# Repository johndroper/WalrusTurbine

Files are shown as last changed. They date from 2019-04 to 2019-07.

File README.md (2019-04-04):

# The Walrus Turbine Procedural Engine
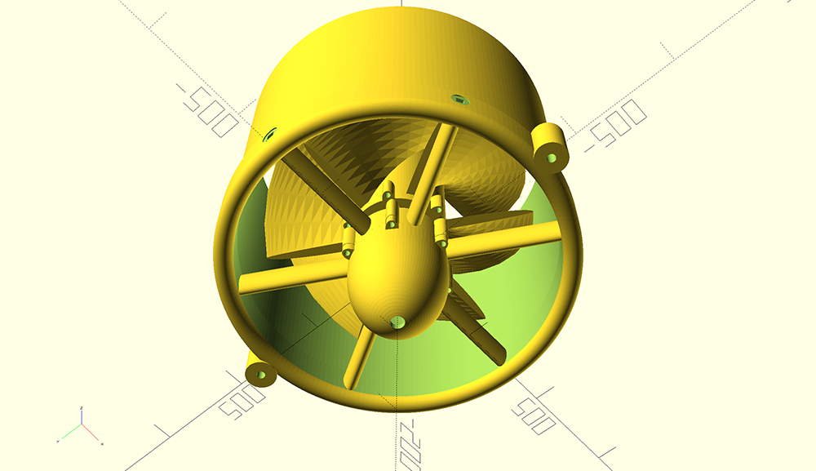
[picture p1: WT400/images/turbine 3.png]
Turbine


WalrusTurbine is a procedural engine for making mostly 3D printable mobile hydroelectric power generators.  

## Getting Started

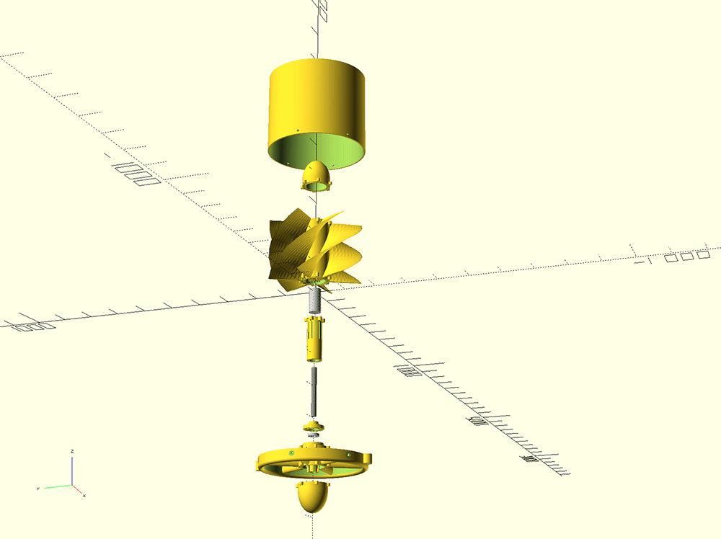
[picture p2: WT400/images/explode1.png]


### Prerequisites

The project is written in [OpenSCAD](http://www.openscad.org/).

### Installing

1. Put all .scad files in the same directory.
2. Open [assembly.scad](assembly.scad) in OpenSCAD to see the full assembled model.
3. Set the explode flag to 1, save, and have a look around. This may be just a wee bit taxing on your machine...

## Physical Assembly

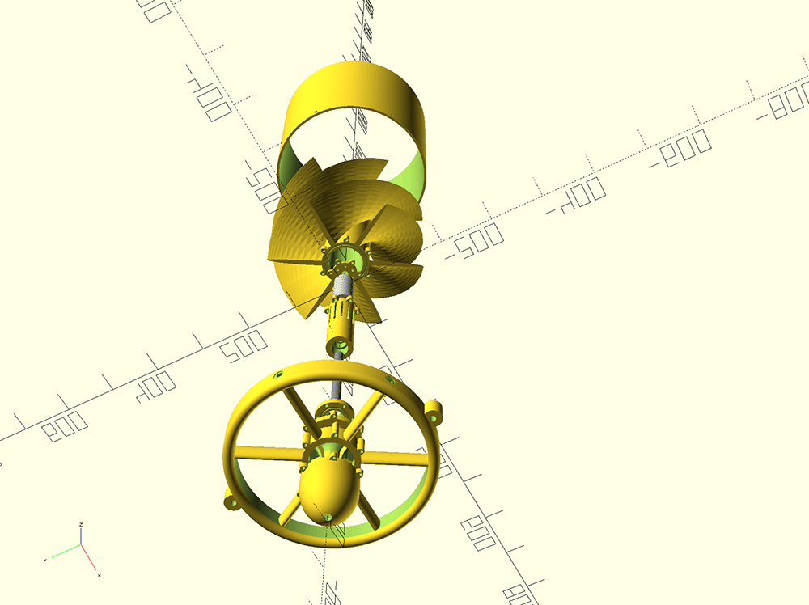
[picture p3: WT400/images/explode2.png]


The Walrus Turbine Procedural Engine was used create a denomstration model called the WT400. The WT400 is design to be printed on a printer with at least 400 mm build volume in all axis.

### Building a WT400
* [List of the non 3d printable parts and where to buy them.](WT400/parts-list.md)
* [Super rudimentary instructions.](WT400/instructions.md)

A lot more docs are coming soon so stay tuned.

## Contributing

Anyone who wants to contribute anything from openSCAD improvements to better assembly instructions is more than welcome.

## Authors

* **John Roper** 
* **Peter Brussard**

## License

This project is licensed under the MIT License - see the [license.txt](license.txt) file for details

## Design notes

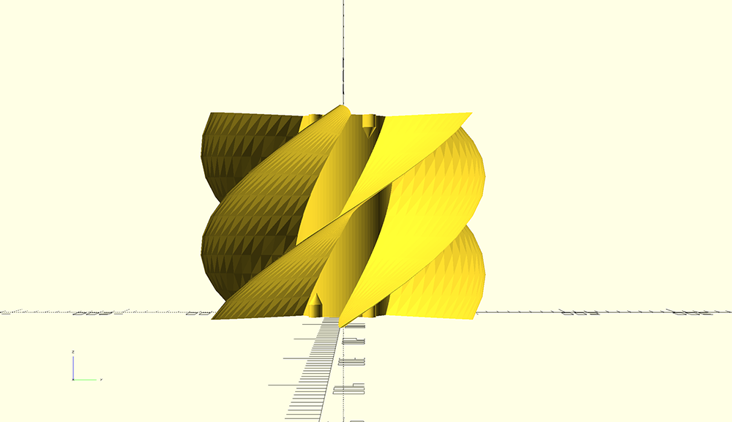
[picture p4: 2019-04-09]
WT400/images/runner front.png

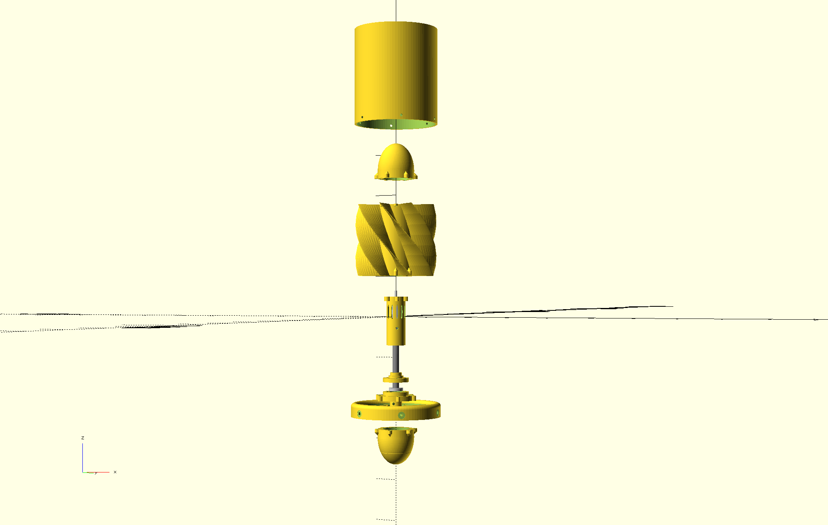
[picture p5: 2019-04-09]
WT400/images/explode 1.png

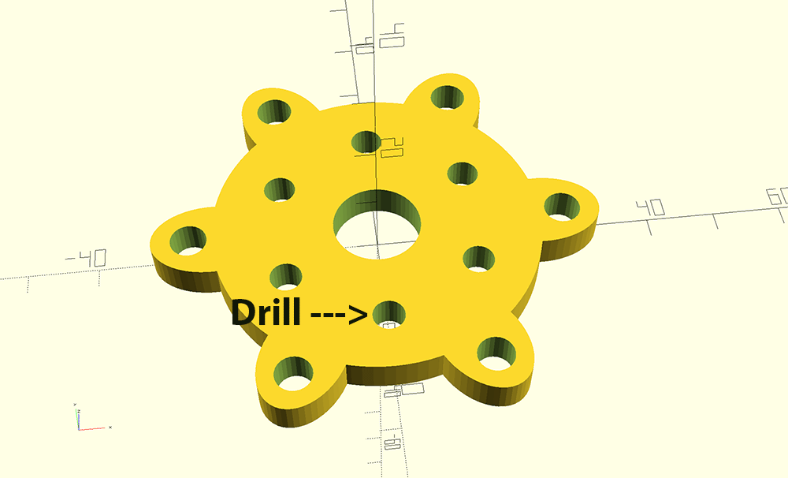
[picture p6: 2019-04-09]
WT400/images/drill_motor_mount_holes.png

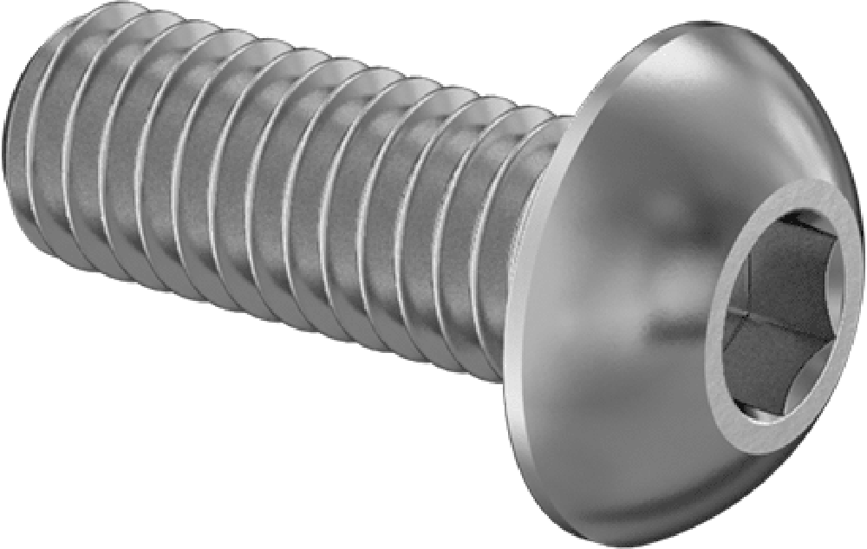
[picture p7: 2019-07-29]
WT400/images/M3_8mm_hex_screw_1000.png

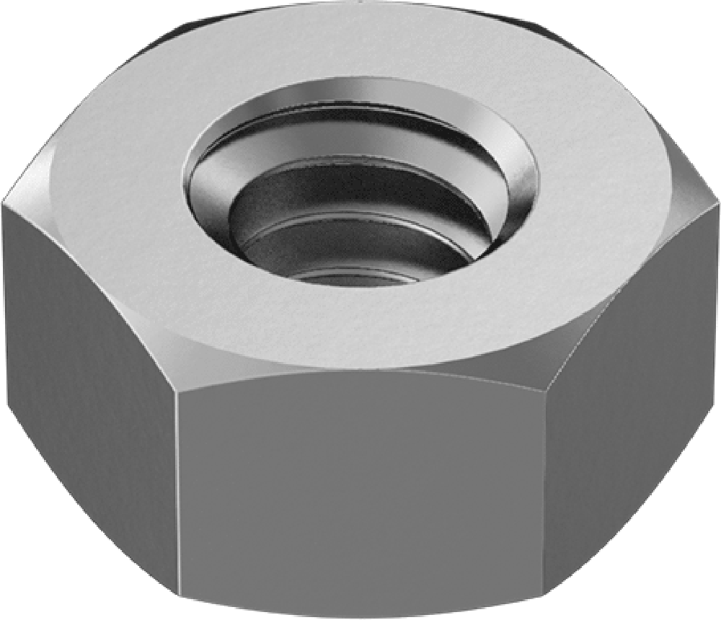
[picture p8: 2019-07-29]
WT400/images/hex_nut_1000.png

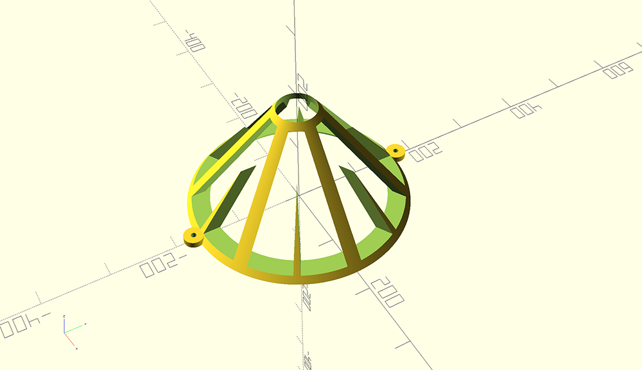
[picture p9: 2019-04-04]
WT400/images/guard.png

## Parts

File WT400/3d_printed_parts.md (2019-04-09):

# WT400 3D Printed Parts

## Parts
|  Part | Closeup  | 
| ---- | ---- |
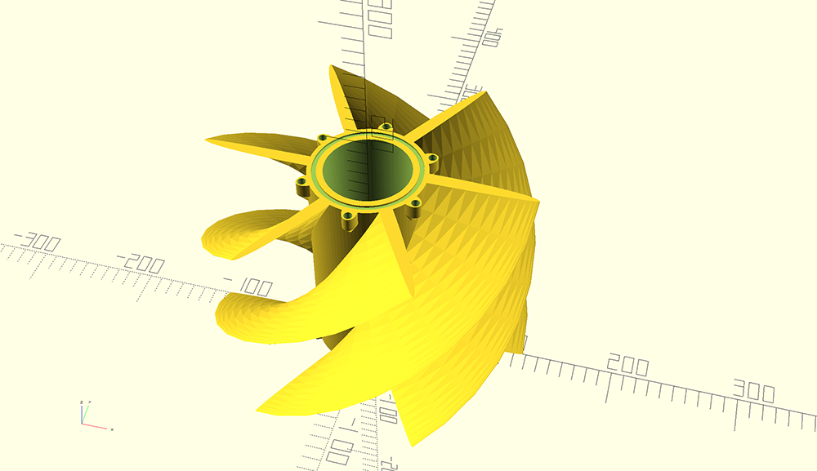
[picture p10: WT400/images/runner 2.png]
Runner
| <a id="runner">Runner</a> |  |
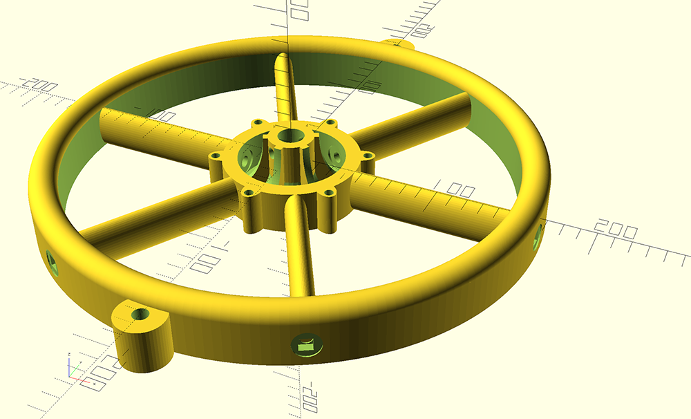
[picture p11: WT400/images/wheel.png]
Wheel
| <a id="wheel">Wheel</a> |  |
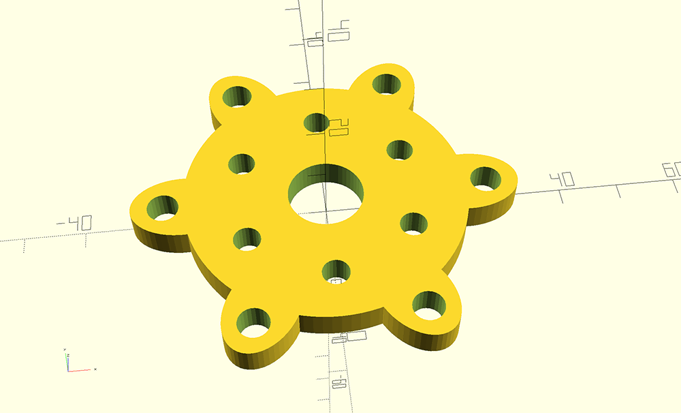
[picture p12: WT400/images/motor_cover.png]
Motor Cover
| <a id="motor_cover">Motor Cover</a> |  |
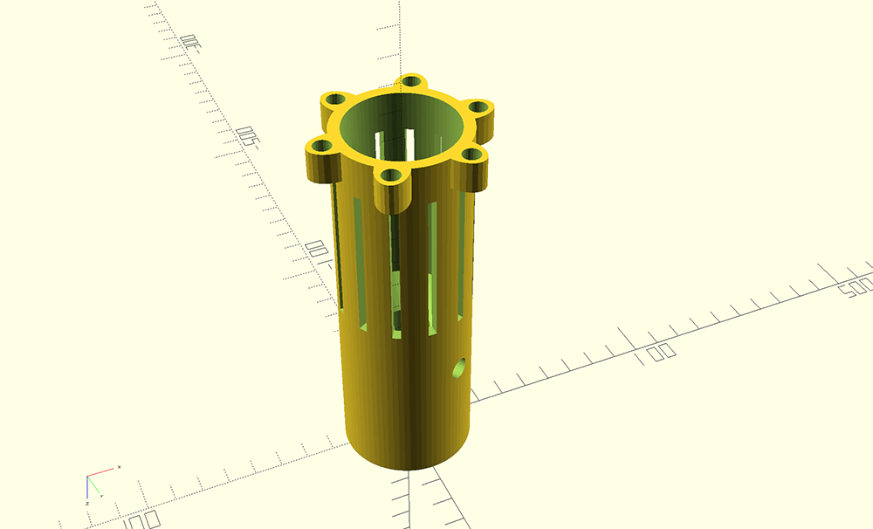
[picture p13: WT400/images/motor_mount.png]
Motor Mount
| <a id="motor_mount">Motor Mount</a> |  |
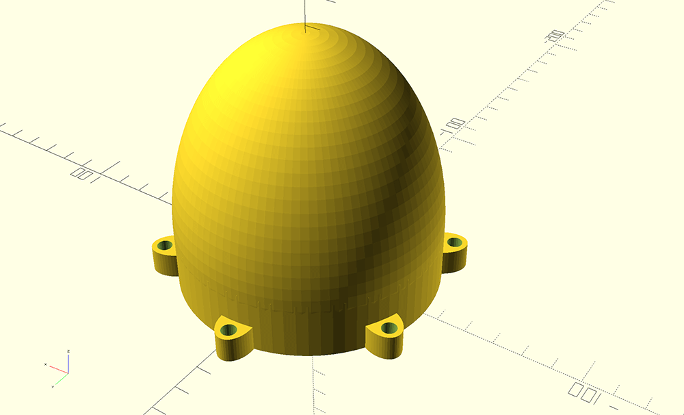
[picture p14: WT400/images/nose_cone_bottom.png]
Nose Cone Bottom
| <a id="nose_cone_bottom">Nose Cone Bottom</a> |  |
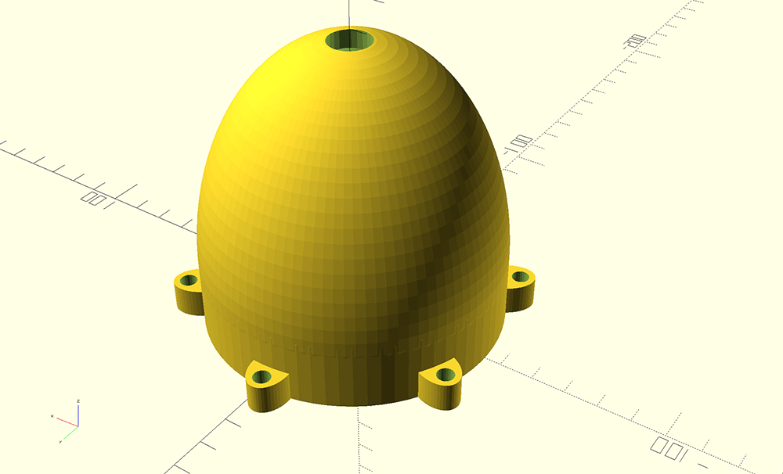
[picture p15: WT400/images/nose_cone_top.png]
Nose Cone Top
|<a id="nose_cone_top">Nose Cone Top</a> |  |
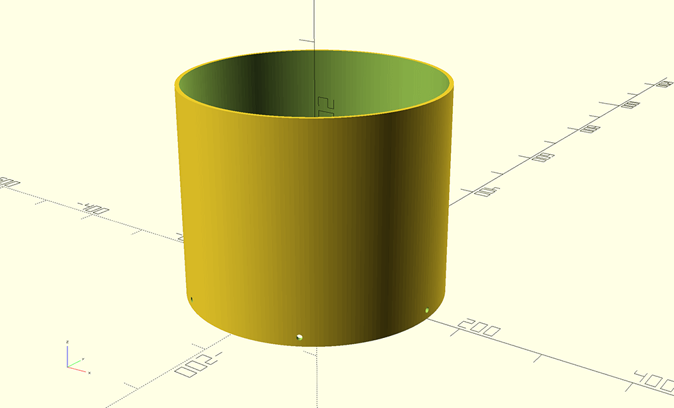
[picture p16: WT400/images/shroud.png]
Shroud
| <a id="shroud">Shroud</a> |  |
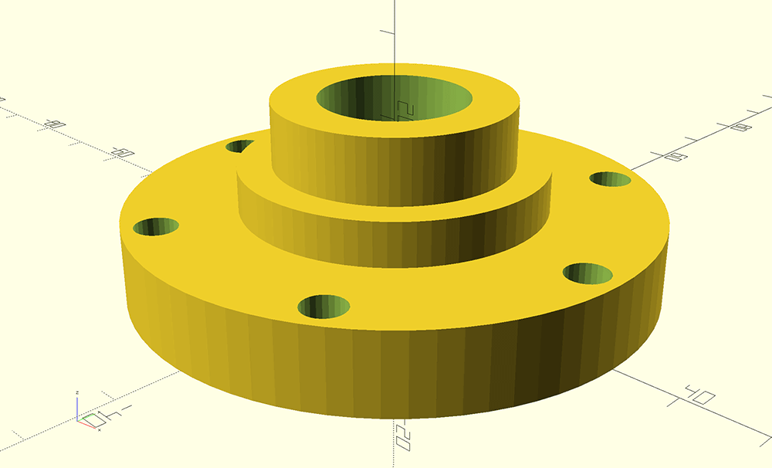
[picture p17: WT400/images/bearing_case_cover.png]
Bearing Case Cover
| <a id="bearing_case_cover">Bearing Case Cover</a> |  |
| <a id="end_cap">End Cap</a> | End Cap |
| <a id="bearing_mount_jig">Bearing Mount Jig</a> | Bearing Mount Jig |
| <a id="shaft_hole_jig">Shaft Hole Jig</a> | Shaft Hole Jig|

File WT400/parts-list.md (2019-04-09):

| Name | Part | Where to buy | # Parts Required |
| --- | ----- | ---- | --- |
| <a id="grease_seal">Grease Seal</a> ||[Grease Seal for 5/8" Diameter Rotary Shaft](https://www.mcmaster.com/5154T83") | 2 |
| <a id="aluminum_round_tube">Shaft</a> ||[6061 Aluminum Round Tube](https://www.mcmaster.com/9056K91") | 1 |	
| <a id="thrust_bearing">Thrust Bearing</a> || [Thrust Ball Bearing](https://www.mcmaster.com/6655K38") |	1 |	
| <a id="ball_bearing">Rotory Bearing</a> ||[Ball Bearing](https://www.mcmaster.com/60355K506") | 1 |
| <a id="hex_head_screw_1_1_2_inch">1-1/2" Hex Bolt</a> ||[18-8 Stainless Steel Hex Head Screw 1/4"-20 1-1/2"](https://www.mcmaster.com/92198a546") | 1 |
| <a id="carriage_bolt">Carriage Bolt</a> | |[18-8 Stainless Steel Square-Neck Carriage Bolt 1/4"-20 5-1/2"](https://www.mcmaster.com/92356A564") | 6 |
| <a id="screw_8_32_5_8">8-32 5/8" Hex Screw</a> | |[18-8 Stainless Steel Button Head Hex Drive Screw 8-32 5/8"](https://www.mcmaster.com/92949A196") | 12 |
| <a id="screw_8_32_1_2">8-32 1/2" Hex Screw</a> ||[18-8 Stainless Steel Button Head Hex Drive Screw 8-32 1/2"](https://www.mcmaster.com/92196A194") | 12 |
| <a id="screw_4_40">4-40 3/4" Hex Screw</a> | |[18-8 Stainless Steel Button Head Hex Drive Screw 4-40 3/4"](https://www.mcmaster.com/92949A113") | 6	|
| <a id="M3_8mm_hex_screw">M3 8mm Hex Screw</a> ||[18-8 Stainless Steel Button Head Hex Drive Screw M3 8mm](https://www.mcmaster.com/92095A181") | 6 |	
| <a id="screw_1_4_2">2" Hex Bolt</a> | |[18-8 Stainless Steel Hex Head Screw 1/4"-20 2"](https://www.mcmaster.com/92198A550") | 1 |	
| <a id="hex_nut">Hex Nut</a> | |[18-8 Stainless Steel Hex Nut 1/4"-20](https://www.mcmaster.com/91845A029") | 10 |	
| <a id="washer">Washer</a> ||[18-8 Stainless Steel Washer for 1/4" Screw Size, 0.281" ID, 0.625" OD](https://www.mcmaster.com/92141A029") | 10 |	
| <a id="heatset_inserts">Heat-Set Inserts</a> | |[Heat-Set Inserts for Plastics 8-32](https://www.mcmaster.com/93365A142") | 24 |	
| <a id="spring">Spring</a> ||[Compression Spring 1" Long, 0.845" OD](https://www.mcmaster.com/9657K319") | 1 |	
| <a id="orings_3">3 1/4" O-Ring</a> ||[Oil-Resistant Soft Buna-N O-Rings 3 1/4 OD](https://www.mcmaster.com/2418T189") | 2 |	
| <a id="1_7_8_oring">1 7/8" O-Ring</a> ||[Oil-Resistant Soft Buna-N O-Rings 1 7/8 OD](https://www.mcmaster.com/2418T178") | 1 |	
| <a id="motor">Motor</a> | |[uxcell 12V DC 200 RPM Gear Motor](https://www.amazon.com/gp/product/B01KTXRB90/?ie=UTF8&psc=1&tag=walrusturbine-20") | 1 |	
| <a id="hub">Motor Mounting Hub</a> ||[Pololu 1083 UNIVERSAL ALUMINUM MOUNTING HUB](https://www.amazon.com/gp/product/B00B887FX8/?ie=UTF8&psc=1&tag=walrusturbine-20") | 1 |	
| <a id="eye_bolt">Eyebolt</a> | |[Routing Eyebolt with Nut 1/4"-20 Thread, 2-1/2" Shank](https://www.mcmaster.com/9489t21) | 2  
| <a id="wire">Speaker Wire</a> ||[AmazonBasics 16-Gauge Speaker Wire - 100 Feet](https://www.amazon.com/gp/product/B006LW0W5Y/?ie=UTF8&psc=1&tag=walrusturbine-20") | 1 |	
| <a id="pla">PLA</a> | |[HATCHBOX PLA 3D Printer Filament, 1 kg Spool, 1.75 mm](https://www.amazon.com/HATCHBOX-3D-Filament-Dimensional-Accuracy/dp/B00J0ECR5I/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") | 4 |	
| <a id="grease">Grease</a> ||[CRC SL3121 Marine Boat Trailer and 4 x 4 Wheel Bearing Grease - 14 wt. oz.](https://www.amazon.com/gp/product/B000CPJMY8/?ie=UTF8&psc=1&tag=walrusturbine-20") | 1 |	
| <a id="spray">Clear Glaze</a> ||[Krylon I00500A00 12-Ounce Triple Thick Clear Glaze Aerosol Spray](https://www.amazon.com/gp/product/B001144TJC/?ie=UTF8&psc=1&tag=walrusturbine-20") | 1 |	
| <a id="masking_tape">Masking Tape</a> || [Scotch(R) Home and Office Masking Tape 3436-3, 3/4-inch x 54.6 Yards, 3 Pack](https://www.amazon.com/Scotch-Office-Masking-3436-3-4-inch/dp/B00347A8E4/?ie=UTF8&psc=1&tag=walrusturbine-20") | 1 |
| <a id="loctite">Loctite</a> | | [Loctite Heavy Duty Threadlocker, 0.2 oz, Blue 242, Single](https://www.amazon.com/Loctite-Heavy-Duty-Threadlocker-Single/dp/B000I1RSNS/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") | 1 |
| <a id="caulk">Caulk</a> || [Gorilla Clear 100 Percent Silicone Sealant Caulk, Waterproof and Mold & Mildew Resistant, 10 ounce Cartridge, Clear, (Pack of 1)](https://www.amazon.com/Gorilla-Silicone-Waterproof-Resistant-Cartridge/dp/B01MQW8AEM/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") | 1 |

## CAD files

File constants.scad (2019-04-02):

shaft_height = 152.4;
shaft_diameter = 15.875;
spring_height = 25.4;
thrust_bearing_od = 28.575;
thrust_bearing_id = 15.9512;
thrust_bearing_height = 8.6868;
motor_offset = 0;
motor_diameter = 37;
motor_height = 75; //60;
motor_mount_od = 47; 
thrust_bearing_mount_height = thrust_bearing_height + 20 + spring_height;
echo(thrust_bearing_mount_height=thrust_bearing_mount_height);
motor_mount_height = motor_height + thrust_bearing_mount_height + 5; 
echo(motor_mount_height=motor_mount_height);
core_diameter = 90;
core_radius = core_diameter / 2;
cone_height = 35;
core_cutout = 33;
seal_diameter = 31.75;
seal_height = 6.7564;
rotary_bearing_height = 7.14375;
rotary_bearing_diameter = 34.925;
end_cap_height = seal_height + rotary_bearing_height + 7;
echo(end_cap_height=end_cap_height);

bearing_case_cover_height = seal_height + 13;
motor_cover_height = 5;
core_height = motor_mount_height + bearing_case_cover_height + end_cap_height + motor_cover_height + 14;
echo(core_height =core_height);

runner_height = core_height + cone_height;
echo(runner_height=runner_height);
cone_nut_offset = 30;


blade_length = 195; // 155;
blade_twist = -120;
blades = 6;

shroud_od = 315;
echo(shroud_od=shroud_od);
shroud_id = shroud_od - 10;
shroud_width =  shroud_od - shroud_id;
shroud_thickness = 10;

shaft_mount_height = 28;
shaft_screw_diameter = shaft_diameter;
shaft_height = 152.4;

spoke_bolt_head_height = 3.9624;

threaded_insert_height = 7.9248;
threaded_insert_diameter_top = 5.9436 + .5;
threaded_insert_diameter_bottom = 5.2832 + .5;
bolt_diameter = 4.1656 + 1;

o_ring_od = 82.8548;
o_ring_id = 75.7936;
o_ring_groove_depth = 3.5306/2 - .25;

small_oring_od = 47.9298;
small_oring_id = 40.8686;

number_of_struts = 6;

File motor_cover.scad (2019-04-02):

include <constants.scad>;

motorCover();

module motorCover()
{
    difference()
    {
        union()
        {
            cylinder(
                d=motor_mount_od, 
                h=5,
                $fn=100);

            //bolt stands
            for(i=[0:60:360])
            {
                rotate([0,0,i])
                translate([
                    motor_mount_od / 2 ,
                    0,
                    0])
                {
                    scale([1.5,1,1])
                    cylinder(
                        d=threaded_insert_diameter_top + 5,
                        h=5,
                        $fn=50);
                    
                }
            }
        }
        
        //motor shaft hole
        translate([0,0,-.01])
        cylinder(d=12 + .5,h=5 + .02,$fn=50);

        //motor mount holes  
        for(i=[30:60:390])
        {
            rotate([0,0,i])
            translate([
                15.5,
                0,
                -.01])
            {
                cylinder(
                    d=3 + 1.5,
                    h=5+.02,
                    $fn=25);
                
            }
        }

        //bolt holes
        for(i=[0:60:360])
        {
            rotate([0,0,i])
            translate([
                motor_mount_od / 2 + (threaded_insert_diameter_top / 2),
                0,
                -.01])
            {
                cylinder(
                    d=bolt_diameter,
                    h=5+.02,
                    $fn=25);
                
            }
        }
    }
}

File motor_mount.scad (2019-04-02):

include <constants.scad>;

rotate([180,0,0])
motorMount();

module motorMount()
{
    difference()
    {
        union()
        {    
            cylinder(
                d=motor_mount_od, 
                h=motor_mount_height,
                $fn=75);
            
            //threaded insert stands
            for(i=[0:60:360])
            {
                rotate([0,0,i])
                translate([
                    motor_mount_od / 2 ,
                    0,
                    motor_mount_height - threaded_insert_height - 3])
                {
                    scale([1.50,1,1])
                    cylinder(
                        d=threaded_insert_diameter_top + 5,
                        h=threaded_insert_height + 3,
                        $fn=25);
                    
                }
            }
        }

        //motor cutout
        translate([0,0,motor_mount_height-motor_height])
        cylinder(
            d=motor_diameter + 2, 
            h=motor_height + .01,
            $fn=75);

        //threaded insert holes
        for(i=[0:60:360])
        {
            rotate([0,0,i])
            translate([
                motor_mount_od / 2 + (threaded_insert_diameter_top / 2) ,
                0,
                motor_mount_height - threaded_insert_height - 4 ])
            {
                cylinder(
                    r2=(threaded_insert_diameter_top/2),
                    r1=(threaded_insert_diameter_bottom/2),
                    h=threaded_insert_height + 4 +.01,
                    $fn=25);
                
            }
        }
        
        //thurst bearing cutout
        translate([0,0,-1])
        cylinder(
            d=thrust_bearing_od + 1, 
            h=thrust_bearing_height + (spring_height / 2),
            $fn=50);
        
        //spring cutout
        translate([0,0,thrust_bearing_height - .01])
        cylinder(
            d=21.463 + 1, 
            h=spring_height,
            $fn=50);

        //over-hang removal 
        translate([0,0,thrust_bearing_mount_height - 5])
        cylinder(
            r1=(shaft_diameter / 2) , 
            r2=(motor_diameter + 2) / 2 ,
            h=10+.01,
            $fn=50);

       //Shaft Hole
        translate([0,0,-1])
        cylinder(
            d=shaft_diameter + 1.5, 
            h=motor_mount_height,
            $fn=50);
        
        //pin hole
        //for 1/4" x 2" pin
        rotate([0,0,30])
        translate([
            0,
            25.4,
            thrust_bearing_height + spring_height + 8])
        rotate([90,0,0])
        cylinder(
            d=6.35 + 1.5,
            h=50.8,
            $fn=25);
            
        //vents
        for(i=[0:30:360])
        {
            rotate([0,0,i+30])
            translate([
                motor_mount_od/2 - 10,
                -1.5,
                65])
            cube(size=[10,3,motor_height - 20]);  
            //rotate([0,90,0])
//            resize([motor_height - 25,5,10])
//            difference()
//            {
//            cylinder(r=5, h=10, $fn=50);                        
        }
    }
}

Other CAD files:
wheel.scad
assembly.scad
bearing mount jig.scad
bearing_case_cover.scad
end_cap.scad
guard.scad
nose_cone.scad
runner.scad
shaft hole jig.scad
shroud.scad

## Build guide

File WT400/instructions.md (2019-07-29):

# Walrus Turbine 400 Assembly Instructions

## Parts

* [3D Printed Parts List](3d_printed_parts.md)
* [Non 3D Printed Parts & Supplies](parts-list.md)

## Required Tools
* Hand drill
* 3/16" drill bit
* 5/32" drill bit
* ¼” drill bit

## Assembly Steps
1. Parts Prep
    1. Drill outs
       1. Drill out [hex bolt hole](images/motor_mount_hex_bolt_hole.png) in middle of [motor mount](3d_printed_parts.md#motor_mount) with 3/16" drill bit.
       1. Drill out [hex bolt hole](images/wheel_center_hex_bolt_hole.png) in center of [wheel](3d_printed_parts.md#wheel) with 3/16" drill bit.
       1. Drill out 6 [carriage bolt holes](images/carriage_bolt_holes.png) in [wheel](3d_printed_parts.md#wheel) with ¼” drill bit.
       1. Drill out 6 [motor mount holes](images/drill_motor_mount_holes.png) in [motor cover](3d_printed_parts.md#motor_cover) with 5/32" drill bit.
    1. Masking heat-set insert holes
        1. Cover 6 [heat-set insert holes](images/runner_top_heatset_masks.png) on top of [runner](3d_printed_parts.md#runner) with [masking tape](3d_printed_parts.md#masking_tape).
        1. Cover 6 [heat-set insert holes](images/runner_bottom_insert_masks.png) on bottom of [runner]( 3d_printed_parts.md#runner) with [masking tape](3d_printed_parts.md#masking_tape).
        1. Cover 6 [heat-set insert holes](images/motor_mount_bottom_masks.png) on [motor mount](3d_printed_parts.md#motor_mount) with [masking tape](3d_printed_parts.md#masking_tape).
        1. Cover 6 [heat-set insert holes](images/wheel_center_insert_masks.png) on [wheel](3d_printed_parts.md#wheel) with [masking tape](3d_printed_parts.md#masking_tape) .
    1. Glazing 3D printed parts
       1. In a well ventilated area, spray one side of all 3D printed parts (2 coats) with [clear glaze](parts-list.md#spray).
       1. Let parts dry 24 hours.
       1. Turn parts over, spray other side of all 3D printed parts (2 coats) with [clear glaze](parts-list.md#spray).
       1. Let parts dry 24 hours.
    1. Installing [heat-set inserts](parts-list.md#heatset_inserts)
        1. Install 6 heat-set inserts in [top of runner](images/runner_top.png). 
        1. Install 6 heat-set inserts in [bottom of runner](images/bottom_of_runner.png).
        1. Install 6 heat-set inserts in [motor mount](3d_printed_parts.md#motor_mount).
        1. Install 6 heat-set inserts in [wheel](3d_printed_parts.md#wheel). 
1. Center Shaft Assembly
    1. Drill ¼” holes in [shaft](parts-list.md#aluminum_round_tube) 12 mm on center from each end using [shaft hole jig](3d_printed_parts.md#shaft_hole_jig).
    1. Be sure to remove any burrs from hole.
    1. Mount [rotary bearing](parts-list.md#ball_bearing) on [shaft](parts-list.md#aluminum_round_tube) 79 mm from end to top of bearing using [bearing mount jig](3d_printed_parts.md#bearing_mount_jig).
    1. Cover ends of [shaft](parts-list.md#aluminum_round_tube) with [masking tape](parts-list.md#masking_tape).
1. End Cap Assembly
    1. Mount [grease seal](parts-list.md#grease_seal) in [end cap](3d_printed_parts.md#end_cap) and [bearing case cover](3d_printed_parts.md#bearing_case_cover).
    1. Apply [grease](parts-list.md#grease) to inside surfaces of both parts including o-ring grooves.
    1. Be sure to fill empty space between both seals and the bearing with grease.  
    1. Insert [rotary ball bearing](parts-list.md#ball_bearing) and [shaft](parts-list.md#aluminum_round_tube) assembly into [end cap](3d_printed_parts.md#end_cap). 
    1. Insert [1 7/8" o-ring](parts-list.md#1_7_8_oring) into groove on [end cap](3d_printed_parts.md#end_cap).
    1. Mount [bearing case cover](3d_printed_parts.md#bearing_case_cover) onto [shaft](parts-list.md#aluminum_round_tube).
    1. Secure [bearing case cover](3d_printed_parts.md#bearing_case_cover) to [end cap](3d_printed_parts.md#end_cap) with 6 [8-32 5/8" hex screw](parts-list.md#8-32_hex_screw).
1. End Cap Install
    1. Slide [thrust bearing](parts-list.md#thrust_bearing) onto [shaft](parts-list.md#aluminum_round_tube) below [bearing case cover](3d_printed_parts.md#bearing_case_cover).
    1. Grease between each layer of [thrust bearing](parts-list.md#thrust_bearing).
    1. Place [3 1/4" o-ring](parts-list.md#orings_3) in groove on [end cap](3d_printed_parts.md#end_cap).
    1. Put [spring](parts-list.md#spring) in top of [motor mount](3d_printed_parts.md#motor_mount).
    1. Slide [motor mount](3d_printed_parts.md#motor_mount) onto [shaft](parts-list.md#aluminum_round_tube), compressing [spring](parts-list.md#spring) until hole in [shaft](parts-list.md#aluminum_round_tube) and [motor mount](3d_printed_parts.md#motor_mount) align.  Then insert [¼-20 2” hex-head bolt](parts-list.md#hex_head_screw_2_inch) through hole in [motor mount](3d_printed_parts.md#motor_mount) and [shaft](parts-list.md#aluminum_round_tube).  Secure with [¼” hex nut](parts-list.md#hex_nut).  
1. Mounting Motor
    1. Install [motor cover](3d_printed_parts.md#motor_cover) on [motor](3d_printed_parts.md#motor) using 6 [M3 x 8mm hex screws](parts-list.md#M3_8mm_hex_screw).
    1. Mount [motor mounting hub](parts-list.md#hub) onto motor shaft with two grub screws. Dab each grub screw hole with [loctite](parts-list.md#loctite) before inserting.
    1. Slide [speaker wire](parts-list.md#wire) down inside of [shaft](parts-list.md#aluminum_round_tube) starting at [end cap](3d_printed_parts.md#end_cap) and exiting out [motor mount](3d_printed_parts.md#motor_mount).
    1. Solder [speaker wire](parts-list.md#wire) to [motor](parts-list.md#motor) leads.
    1. Insert [motor](parts-list.md#motor) into [motor mount](3d_printed_parts.md#motor_mount) and secure [motor cover](3d_printed_parts.md#motor_cover) to the [motor mount](3d_printed_parts.md#motor_mount) with 6 [8-32 ½” hex screws](parts-list.md#screw_8_32_1_2).
1. Runner Assembly
    1. Appy [grease](parts-list.md#grease) to [runner](3d_printed_parts.md#runner) top o-ring groove.
    1. Place [motor mount](3d_printed_parts.md#motor_mount) / [end cap](3d_printed_parts.md#end_cap) assembly inside [runner](3d_printed_parts.md#runner).
    3. Align motor hub with holes in bottom of [runner](3d_printed_parts.md#runner) and secure with 6 [4-40 ¾” hex screws](parts-list.md#4-40_hex_screw).
    1. Secure [end cap](3d_printed_parts.md#end_cap) to [runner](3d_printed_parts.md#runner) with 6 [8-32 ½” hex screws](parts-list.md#screw_8_32_1_2).
    1. Wipe up excess grease.
1. Bottom Cone Assembly
    1. Appy [grease](parts-list.md#grease) to [bottom nose cone o-ring groove]() and [runner bottom o-ring groove](images/runner_bottom_oring_groove.png).
    1. Install [3 1/4" o-ring](parts-list.md#3_inch_orings) in [runner bottom o-ring groove](images/).
    1.  Secure [bottom nose cone](3d_printed_parts.md#bottom_nose_cone) to [runner](3d_printed_parts.md#runner) with 6 [8-32 ½” hex screws](parts-list.md#8-32_hex_screw).
    1. Wipe up excess grease. 
1. Wheel Assembly
    1. Feed [speaker wire](parts-list.md#wire) through center of wheel.
    1. Insert free end of [shaft](parts-list.md#aluminum_round_tube) through [center of wheel](images/wheel_center.png) and align ¼" hole in [shaft](parts-list.md#aluminum_round_tube) with [¼" hole in center section of wheel](images/wheel_hex_bolt_hole_align.png). 
    1. Insert [¼-20 1 ½” hex head bolt](parts-list.md#hex_head_screw_1_1_2_inch) through [¼" hole in wheel](images/wheel_hex_bolt_hole.png) and [shaft](parts-list.md#aluminum_round_tube) and secure with [¼” hex nut](parts-list.md#hex_nut).
    1. Insert [shroud](3d_printed_parts.md#shroud) into [slot on underside of wheel](images/wheel_slot.png) and align [shroud holes](images/shroud_holes.png) to [wheel carriage bolt holes](images/wheel_carriage_bolt_holes.png).
    1. Insert [¼-20 5 ½” carriage bolts](parts-list.md#carriage_bolt) into [wheel carriage bolt holes](images/wheel_carriage_bolt_holes_2.png) and secure with [¼” washer](parts-list.md#washer) and [hex nut](parts-list.md#hex_nut).
    1. Liberally fill in [shaft](parts-list.md#aluminum_round_tube) around [speaker wire](parts-list.md#wire) with [caulk](parts-list.md#caulk).
    1. Secure [top nose cone](3d_printed_parts.md#nose_cone_top) to wheel using 6 [8-32 ½” hex screws](parts-list.md#screw_8_32_1_2).
    1. Fill around [speaker wire](parts-list.md#wire) in top cone hole with [caulk](parts-list.md#caulk).

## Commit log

2019-04-02 Inital commit
    Inital commit. Mostly cleaned up dir and added license file.
    [assembly.scad, bearing mount jig.scad, bearing_case_cover.scad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]
2019-04-03 more wt400 instructions
    [assembly.scad]
2019-04-04 more work on assembly instructions
    [assembly.scad]
